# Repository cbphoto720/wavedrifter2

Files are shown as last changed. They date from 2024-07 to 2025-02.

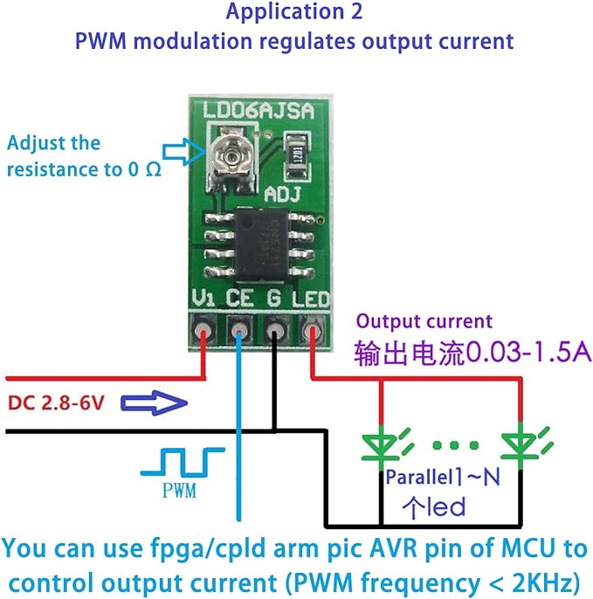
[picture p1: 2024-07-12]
Electronics/LED_driver.jpg

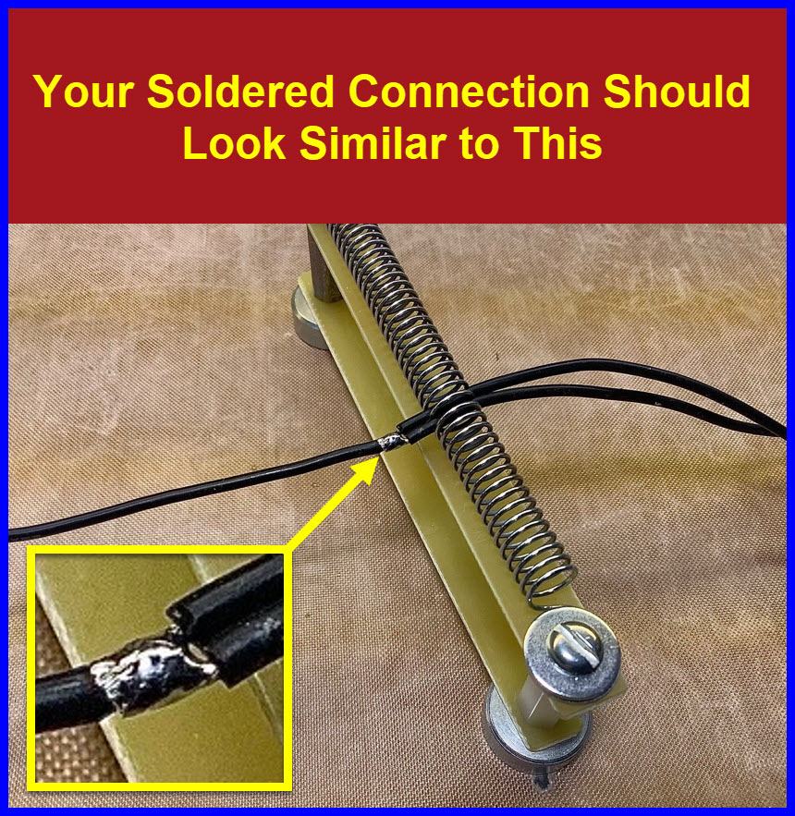
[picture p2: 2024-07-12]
Electronics/D.jpg

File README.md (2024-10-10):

# WIP
- [ ] LoRA underwater trails!! See [links on this page](https://www.thethingsnetwork.org/forum/t/lora-under-water/41144/26?page=2)
- [x] solder recovery LED to test on breadboard
- [x] more clearance for coin cell bat on sparkfun M8P board
- [x] FIGURE OUT GPS/ICM CONNECTION ISSUES
- [ ] write a new file if GPS / IMU log get too big?
- [x] Test the drifter2 Voltage sketch to see if it correctly reads the input voltage
- [ ] check which the best clock speed for teensy to run
- [ ] work on GPS buffer and timing
- [ ] work on more commands to send (beep 1s, recovery mode, flash LED 50% 1s)

- [x] Come up with solution for QWIIC connector issues
	- plug it in harder :)
- [ ] Come up with timing scheme for not overlapping GPS, IMU, and SD writes.  RFM broadcast needs to be its own thing.
- [ ] fix buf[99] vs buf[100] error that causes extra spaces
- [ ] SD card writing scheme that SAVES ON POWER DOWN
- [ ] write RAWX data to SD card (whole thing??? can the M8P make some UBX files?)
	- [ ] [write data to SD card efficiently](http://elm-chan.org/docs/mmc/mmc_e.html) and [also this one](https://stackoverflow.com/questions/25837386/read-write-binary-data-on-sd-using-arduino)
- [ ] BE CAREFUL USING RECOVERY LED AS SIGNAL LED (could draw too much current if PWM doesn't work)
- [ ] voltage divider to measure battery life
	- modify power battery connection to have a splitter for resistors and for the power board
	- **Low Voltage -> activate recovery mode**
	- **Extreme Voltage - > Shut down rover** (may only be able to do sleep mode)
	- design a power delivery pcb that has voltage monitoring, Hal effect sensor ON/OFF, and RFM filtering built in!
- [ ] 3DP new internalmounts 5.2
- [x] Manufacture drifter2.1
- [ ] Base station code to run into mission planner
- view GPS updates
- [ ] post photos and write assembly guide

# Code
### Speed
**RFM**
- test if using strlen is faster than using sizeof buffer.  (better to send the null chars or to calculate message size before sending it)

# Tests
- [ ] buoyancy test of drifter2.0
- [ ] buoyancy test of drifter2.1
- [ ] GPS underwater test
- [ ] RFM underwater test
# Nice-to-haves
- [ ]  design power/signal delivery pcb as a hat for teensy to make connections easier
- [ ] design new GPS antenna mount
- [ ] stronger mounting of IMU
- [ ] recovery LED mounting position
- [ ] [IMU FIFO buffer information](https://web.archive.org/web/20240229060544/https://wolles-elektronikkiste.de/en/icm-20948-9-axis-sensor-part-ii)
____
- [x]  cut the red wire inside one of your microUSB cables.  Use jumpers and power supply to spin up the box
- RFM69 should be power by teensy onboard 3V supply (Likely cleaner than the FlipFlop board)
- [x]  Internal mounts is just slightly too tall.  take off 0.5 or 1mm and include a cutout for the Teensy 4.0 backing SMD electronics.
- [ ] add mounts for Status LED, Recovery LED, Buzzer
- [ ] [RAWX message structure](https://docs.ros.org/en/noetic/api/ublox_msgs/html/msg/RxmRAWX.html)
- [x] u-center M8P config
	Only output NEMA strings and RAWX data
	[10Hz U-blox binary GPS data in 66 lines of code (arduino)](https://www.youtube.com/watch?v=TwhCX0c8Xe0&t=0s)
	save configuration so that it can be uploaded to each board.  (have arduino read a ublox startup file???  That would be the cleanest way to ensure the boards are config ready)
	then work on arduino parsing of the hex binary
- [ ] Interrupt based programming routine so that you know when the buffer is being used!  (dont want to have another message write over the buffer before you read it!)
	have a routine handle the interupt code before returning to what you are doing.
	- look up simple arduino examples of interupts
- [ ] [RFM69HCW datasheet](https://cdn.sparkfun.com/datasheets/Wireless/General/RFM69HCW-V1.1.pdf) Page 48 describes DIO mapping in order to select what type of interrupt you would like to know about the buffer.  This is useful for Interrupt routines to handle saving the data

- [ ] Write code to test RFM 
- [ ] test broadcast with different drifter SG & range
- [ ] Another test of speed by broadcasting IMU data live
- [x] Do not work on HousingMounts until you finalize what electronics you need.  (3d printed inside)
	top of battery can sit 16mm from the top of 2-140_UP internalring.
	O-ring crossed & stretched 10mm from top of arduino board
- [ ] Code that detects a large upsurge in waves (perhaps a good time to broadcast/look for GPS on the crest of a wave???)

- [x] UPDATE FALK
	- Housing final size
		- USE [F9P board](https://gnss.store/zed-f9p-gnss-modules/145-195-elt0128.html#/61-gnss_module-l1_l2_zed_f9p) to achieve a 2mm increase in size (smaller battery size too)
	- internal board mount
	- Transceivers are communicating
		- what if the board would receive GPS, Broadcast that is got a hit, then trigger a camera to take a picture as fast as possible since GPS aquisition
	*Questions
	- ask for 3dp company name
	- show code running

###### Housing
- [ ] PCBway 3d print: Somos Ledo resin + UTR-8100 (Translucent) (See if the spray varnish option changes the O-ring dimensions!)
- [x] Finish GPS mount with space for reed switch + LED + RFM board
- [x] place to mount flip flop board
- [x] place to mount buzzer somewhere
- [x] place to mount battery O ring hooks on M8P board
- [x] FLIP SCREWS they wont fit unless the nut is face up

- [x] build in tolerance for inner mating halves
- [x] build in tolerance for o-ring groove (for using a HSS lathe tool to make face grooves)??? **Decide if you are going to use the lathe**

- [x] how to connect lipos (and how to charge)
- [x] find a reed switch/ HAL sensor

- [x] mount board internals

###### Electronics
- [x] solder RFM69HCW boards to propotying pins
- [x] test transceiver boards (follow [this guide](https://learn.sparkfun.com/tutorials/rfm69hcw-hookup-guide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))
- [x] Work on HAL sensor board
- [x] Power solution for M8P + transmitting mssg (current draw getting close to 250 mA)
	- [x] power M8P through USB connector if needed (tap directly into battery through hall effect sensor switch board)
##### FIXME

# Ideas
**Transciever ideas**
- void setup:
	broadcast Drifter#, Voltage, IMUfilename, GPSfilename
- Recovery mode
	activate internal buzzer
	increase RFM broadcast Hz
	activate LED
- Wave-detect transmission
	look at IMU data to detect a wave, use wave as an opportunity to transmit/look for GPS from a taller height off the water
# Componets
- VHB tape: 0.4" x 0.025" (10.16 x 0.635 mm)
## GPS
**glonass**
- 1598-1604 MHz
- GPS 1575 MHz L1

[SMA to U.FL connector](https://www.coaxrf.com/shop/4uflcables/smaconnector/gold-plated-sma-male-plug-to-ipx-u-fl-male-plug-center-rf-adapter-connector/) $5.49

[GNSS OEM F9P board ](https://gnss.store/zed-f9p-gnss-modules/145-195-elt0128.html#/61-gnss_module-l1_l2_zed_f9p)
**L1/L2 Antennas**
- [AHP2258.07.0060A](https://www.taoglas.com/product/active-gnss-l1-l2-band-antenna/) TAOGLAS (slightly too big with PCB) (70x70mm ground plane)
- [ 2JM3201C2F ](https://www.2j-antennas.com/antennas/single-internal-antennas/2jm3201c2f-high-precision-gnss-gps-beidou-galileo-glonass-sbas-rtk-l1-l2-active-stacked-patch-internal-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) 2J Antennas GREAT SIZE (slightly worse but tested W/O groundplane!)
- [ANT1825JB01BGNL2A](https://www.digikey.com/en/products/detail/pulse-electronics/ANT1825JB01BGNL2A/15290928) not a lot of datasheet (TOO BIG MOQ)
- [HP2258.A](https://www.digikey.com/en/products/detail/taoglas-limited/HP2258-A/21777748) Taoglas PASSIVE L1/L2
- [APRG2512F01](https://www.digikey.com/en/products/detail/abracon-llc/APRG2512F01-0100S/15912595) Good datasheet
### Transmitter
- [sparkfun dev board](https://www.sparkfun.com/products/15005)
###### Alternative hardware
- [Ublox NEO-M8P-0](https://www.digikey.com/en/products/detail/u-blox/NEO-M8P-0/6150644)
	- Smaller footprint than ZED-F9P
	- Low power (~35mA [ICC Acquisition. Average current from startup until the first fix])
	- 3V

- [mini usb dev board](https://gnss.store/neo-m8p-gnss-modules/90-elt0078.html)

### Antenna
- [TAOGLAS AGGP.25f](https://www.digikey.com/en/products/detail/taoglas-limited/AGGP-25F-07-0060A/3083243) dual 1.575/1.602GHZ PATCH with U.FL connector.  High beam width for more tilt tolerance

###### RF tranceiver
- [sparkfun transciever](https://www.sparkfun.com/products/13909) 915 or 434MHz comms (500m range in open air)  can remotely activate drifters, receive position, or use an [activate an LED](https://www.mouser.com/ProductDetail/Cree-LED/XPEWHT-L1-0000-00D01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)  (time lapse of wave)
###### Combo antenna GSM / GPS
- internal circumference 188mm
- 1.2 to 1.6 GHz

- [Smallest combo ant](https://www.digikey.com/en/products/detail/te-connectivity-linx/ANT-LPC-FPC-100/10663172) 64mm long
- [ Molex](https://www.digikey.com/en/products/detail/molex/2133530100/11673870) flexible 119mm with 2 U.FL
- [Ceramic patch style](https://www.l-com.com/embedded-active-gps-gsm-3g-antenna-3dBi-5dBic-ufl-hg821-03pu-gps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) 42mm square ground plane
-[ TAOGLAS flex ant](https://www.digikey.com/en/products/detail/taoglas-limited/FXUB70-A-07-C-001/4965533) 150mm long
- [BIG external TAOGLAS](https://www.mouser.com/ProductDetail/Taoglas/MA104.C.AB.015?qs=Ajmft%252BTTukF16yQE2i0Gfw%3D%3D)
###### Alternative hardware
- [page 24](https://content.u-blox.com/sites/default/files/NEO-M8P_HardwareIntegrationManual_UBX-15028081.pdf) of ublox handbook reccomends GPS antenna
	- https://www.tallysman.com/product/tw3400-single-band-gnss-antenna/
	- https://www.digikey.com/en/products/detail/taoglas-limited/GP-1575-25-4-A-02/2332642 (i found this patch antenna through a 1.575GHz digikey filter)
	- https://www.digikey.com/en/products/detail/taoglas-limited/A-40-A-301111/4503583

**Patch antennas**
- [Taoglas](https://www.digikey.com/en/products/detail/taoglas-limited/AP-25F-07-0078A/2754153) 3" U.FL cable (SAW, LNA, LNA) (medium size)
- [Taoglas AP.10F.07.0039B](https://www.digikey.com/en/products/detail/taoglas-limited/AP-10F-07-0039B/3083256) 1" U.FL cable (SAW, LNA, LNA) (smallest package)
- [Taoglas AGGP.25F.07.0060A](https://www.digikey.com/en/products/detail/taoglas-limited/AGGP-25F-07-0060A/3083243) (13 grams, first one I ordered)
- [ a med sized offering AP.12F.07.0045A](https://www.digikey.com/en/products/detail/taoglas-limited/AP-12F-07-0045A/3877418) (wonky radiation pattern)

### Reed switch
- look for latching magnetic reed switch

- [potential option](https://www.mouser.com/ProductDetail/MEDER-electronic-Standex/KSK-1E66-1-BV14501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) (expensive $10)
- [potential ](https://www.digikey.com/en/products/detail/tdk-micronas-gmbh/HAL1502%2520UA/18151531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)(HAL effect switch) HAL 1502
	- use with a relay ([maybe this relay](https://www.digikey.com/en/products/detail/cui-devices/SR5-5V-200-1C/16602072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))
	- google "1a relay through hole 5v"
	- [low profile relay option?](https://www.digikey.com/en/products/detail/panasonic-electric-works/TQ2-L-3V/304092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)
	- [another option](https://www.digikey.com/en/products/detail/omron-electronics-inc-emc-div/G5V-1-T90%2520DC24/6650357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)
	- [low power consumption option?](https://www.digikey.com/en/products/detail/cui-devices/SR5-3V-200-1C/16602081)
	- [Flip Flop switch instructions for MCU sleep](https://www.hackster.io/usini/easy-way-to-put-your-board-to-sleep-5184a2)
	- 
- [Sparkfun latching HAL sensor](https://www.sparkfun.com/products/9312)
- [Sparkfun Reed switch non-latching](https://www.sparkfun.com/products/8642)
- [latching reed switch](https://www.layouts4u.net/electrical-items/switches/latching-reed-switch#:~:text=is%20in%20stock%3F-,Latching%20Reed%20Switch,again%20to%20switch%20it%20off.) with magnet on the outside?

## Batteries
- 3.4 V cutoff voltage

**Old bat**
- [250mah lipo](https://www.amazon.com/EEMB-Battery-Rechargeable-Lithium-Connector/dp/B08FD3V6TF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)

**New Bats**
- [820mah](https://www.amazon.com/EEMB-653042-Rechargeable-Connector-Certified/dp/B082152887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) 44x30.5x6.8mm
- [2000mah](https://www.amazon.com/EEMB-2000mAh-Battery-Rechargeable-Connector/dp/B08214DJLJ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) 56x34.5x10.6mm
- [1100mah](https://www.amazon.com/EEMB-1100mAh-Battery-Rechargeable-Connector/dp/B08FD39Y5R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) 51x34.5x6mm
- [tiny 500mah can fit up to 3](https://www.digikey.com/en/products/detail/tinycircuits/ASR00035/9808767)
- [Tiny 290mah (a little smaller than the 500)](https://www.digikey.com/en/products/detail/tinycircuits/ASR00007/7404517)
- alternative 500mAH supplier [bulk pricing](https://tinycircuits.com/products/lithium-ion-polymer-battery-3-7v-500mah)

[Website for all shapes of battery](https://www.lipolbattery.com/lithium%20polymer%20battery.html): LP883648 is 1600mAH and 48mm longest dimension

## Housing
- [BAL TEC](https://www.precisionballs.com/pictgal.php#hollowsteel) Potential manufacturing source?  Makes all kinds of spheres'
- google search terms "cnc machine sphere hollow"
- [MACRO RING cam filter](https://www.amazon.com/dp/B08XMLK592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) Closure plate for interface?
## CLOSURE SYSTEM

Inspiration:

- https://www.indiamart.com/proddetail/stainless-steel-pipe-clamp-16592394673.html
- https://www.mscdirect.com/product/details/04700365
- THIS IS THE BEST ONE https://www.aliexpress.us/item/2255800979747014.html?gatewayAdapt=glo2usa4itemAdapt
- https://www.grainger.com/product/5DFH4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
- https://www.amazon.com/Stainless-Strengthens-Circular-Fasteners-Clamps/dp/B0B35VBNF4
- binder clip?
- [Hose clamp style with cross dowel nuts](https://www.amazon.com/Stainless-Strengthens-Circular-Fasteners-Clamps/dp/B0B35VBNF4?th=1)
- [Stainless cross dowel nuts](https://www.aliexpress.us/item/3256804059479775.html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)
- WALMART [pipe clamp](https://www.walmart.com/ip/Adjustable-pipe-clamp-hose-clamp-quick-release-round-duct-clamp-quick-pipe-clamp-barrel-clamp-ring-SS-galvanized-80-400mm-dia/1670025789)

**3d Printed inspiration**
- [Aquarium clamp](https://www.reef2reef.com/threads/uv-pipe-clamps.633090/)
- [gopro pipe clamp](https://www.instructables.com/GoPro-Hinged-Pipe-Clamp/)
- [SLS print service](https://www.artisanmodelmakers.co.uk/blog/portfolio-items/3d-printed-automotive-parts/)

## O-RINGS
Housing2_rev2 uses a 2-224 o-ring

- -036 rings are too small diameter (similar to what Falk used)
- 2-142 ID close to 60mm  https://www.mcmaster.com/9452K148/
- should increase o ring size for better sealing
- these 60mm metric rings are a better because they are 50A shore hardness https://www.mcmaster.com/2418T185/

**50a Durometer**
- Grainger [2-146 50A o ring](https://www.grainger.com/product/O-Ring-146-712U13)
- Mcmaster [2-231](https://www.mcmaster.com/2418T186/) or [2-230](https://www.mcmaster.com/2418T185/)
  Mcmaster [2-146](https://www.mcmaster.com/2418T161/) Don't go this small unless you really need to

## LED
- [1.5 W COB LED](https://www.digikey.com/en/products/detail/creeled,-inc./JK3030AWT-P-H50EA0000-N0000001/9974567?utm_adgroup=&utm_source=google&utm_medium=cpc&utm_campaign=Pmax_Shopping_Boston%20Metro%20Category%20Awareness&utm_term=&utm_content=&utm_id=go_cmp-20837509568_adg-_ad-__dev-c_ext-_prd-9974567_sig-Cj0KCQjw0_WyBhDMARIsAL1Vz8t7g8jTEnTvU7pAn2EhZ3dJouXCVCa7Tl-RsGRhepSoWFnkOTOHie8aAs1fEALw_wcB&gad_source=1&gclid=Cj0KCQjw0_WyBhDMARIsAL1Vz8t7g8jTEnTvU7pAn2EhZ3dJouXCVCa7Tl-RsGRhepSoWFnkOTOHie8aAs1fEALw_wcB) run with arduino +extra flip flop board.
- [0.5W LED amazon](https://www.amazon.com/dp/B01CUGACEA/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)

# Programming

### 20240424 Talking with Brian
- 915 mHz band is usually multiplexed frequency hopping.  You don't see all that behind the scenes stuff.
- 2 ways to do it
1. Have the master emit a call that asks a drifter for a transciever update.  (advantage that the timing always works out) (disadvantage: teensy has to be collecting data and listening for master at same time)
2. Have the Teensy collect and collect data and then brief pause to cast out their mssg when it is their time slot.  You have to sync with GPS time.  (maybe even having the base broadcast the most recent GPS time could be an advantage)
### RFM69HCW
[Hookup guide](https://learn.sparkfun.com/tutorials/rfm69hcw-hookup-guide/hardware-overview)
- [Tips for teensy guide](https://forum.pjrc.com/index.php?threads/rfm69w-rfm69hw-transceiver-t3.24576/page-3#post-47264)

[RFM69 Git Library LowPowerLab](https://github.com/LowPowerLab/RFM69)

TRANSMIT MESSAGE:

| D# (Drifter #) | STATUS ('STR' Startup, 'LOG' (recording data), 'REC' (recovery), 'OFF' (shutdown)) | LAT | LON | age (GPS data) | Bat voltage |
| --- | --- | --- | --- | --- | --- |
**ATC - Auto Transmission Control**
- set RSSI floor to at least -60dBm, may want to disable to not try to broadcast too quietly
- [Regulater PSU tutorial sparkfun](https://www.sparkfun.com/tutorials/103)
- 
**CSMA**
- transceiver LISTENS before it tries to TALK.  If 2 radios are actively listening to each other, another raido can mess things up by trying to talk over

**Sparkfun m8p**
- Must ALWAYS be trying to aquire a satellite.

# Solidworks

### Housing2_Boss
- internal sphere radius will need clearance for mating feature

**Mechanical:**

- Talk to Kent about Grinding our own HSS groove tool
- Hemisphere half #2 could have an internal lip to improve mating strength
- 50A durometer O-ring and 1/8" cross section would give us the best change with our space.  Could drop to a 3/32 o-ring if space is required.  (Drifter #1 was 70A durometer, 1/16 ring with an improper groove design) 
- 1mm clearance on o-ring groove (need to make battery decision to reduce O-ring size

# References
- **[minimal-arduino-mavlink-example](https://github.com/patrickelectric/minimal-arduino-mavlink-example)** Code to connect teensy to MissionPlanner

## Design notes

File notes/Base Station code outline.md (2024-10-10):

## Init
- [x]  track num of drifters
- [x]  buffer that tracks the last comm record for each drifter.
## Startup
- [x] connect to mission planner
- [ ] start RFM
- [ ] Broadcast Base UTC time (rfm 255 broadcast to all)

## Loop
- [x] heartbeat
- [x] report drifter health & location
- [ ] send drifter commands (recovery, shutdown, etc.)
- [ ] track last time drifter reached comms

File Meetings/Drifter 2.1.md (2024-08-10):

## Updates
- Drifter 2.1 is operational.
	- Everything is barebones.  Drifter is collecting IMU, RAW GPS, and NMEA GGA data and can broadcast any info we need back to base station.
- 
- Working on MAVLink code to polt data in MissionPlanner
- Working on Bat voltage sensor

## WIP
- Base station in MissionPlanner app
## Questions
- is there any budget left to spend?
	- [ ] new HAL effect sensors (non-latching) (or just design better clearance for the reed switches)
	- [ ] more mini GPS antenna
	- [ ] Passive components (capacitors, Power delivery PCB board? {rout power, caps for RFM, HAL effect sensor SMD})
- Any experience with Sparkfun QWIIC cables?  I am leaning toward soldering everything Point-to-point
-

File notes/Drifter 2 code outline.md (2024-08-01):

### SPI
- microsd
- Transceiver
### I2C
- imu
- GPS
##### Key
//WIP - Things to fix!
//FLAG - Important note
//DEBUG - useful for problem solving
//BLINK - good spots to communicate to user what is happening
//OFF - places where the program should shut down (may be able to reset with Flip-Flop board)
//ERROR - places where an error should be thrown

# WIP
- [x] use struct NMEA_GNGGA to parse data ([follow this tutorial](https://www.youtube.com/watch?v=ylxwOg2pXrc&t=0s)) and then broadcast valid fix lat/lon to base
- [ ] find a way to interally store RAWX in M8P LOG file before writing to SD card
	- [ ] exactly what data needs to be written to the card.  Is it the full RAWX binary every time or can we slim it down?
- [ ] broadcast from 915 mHz
	- why can it read transmissions but not ACK or Broadcast on its own?
- [ ]  Log data to microsd
	- [ ] IMU data format
	- [ ] GPS NMEA strings
- [ ] voltage divider to activate Recovery mode
- [ ] receive messages from BASE to activate other sampling modes

**SD_ReadWrite_example3**
- Working prototype of reading/writing data
- Definite connection issue on the breadboard creating weird null characters, even in the SD card FILENAME (a const char).  I am hoping these missing characters are just a connection problem on the breadboard.
**Drifter2.ino**
- determine when to blink LED and what color for indication (look for //BLINKS in code)
- [x] Write code to create the filename for each drifter (here is a good forum post that has a [file naming sprinrf](https://forum.arduino.cc/t/create-variable-text-file-name-to-be-saved-on-sd-card/1158544/3))
- [ ] change gatherIMUdata (160) to ONLY collect data
	- write function to print IMU data once stored in a buffer of sufficient size

**NEO M8P TX-ready indication**
- super useful for interrupt based programming! [Ublox M8P RecieverDescrProtocol](https://content.u-blox.com/sites/default/files/products/documents/u-blox8-M8_ReceiverDescrProtSpec_UBX-13003221.pdf)
	UBX - CFG - PRT (configure PIO port to Tx ready with kb threshold set)
	UBX - MON - HW (monitor Hardware to see PIO assignments)

___
# Functions
- Parse GNGGA -> see readme in drifter2

# VOID SETUP
**microSD card**
- [x] begin serial
- [x] checkIMU
- [x] init SD card /currently ugly
- [x] calibrateIMU
- [x] initialize files
- [x] make filename "drifterXX_log000X.txt"
- [x] choose max file size (Battery life should automatically limit these files to an acceptable amount)
- [x] init GPS
- [x] initialize GPS settings (set up from default (NMEA messages, RAWX, TX-ready interrupt, Nav Freq 4Hz, Full power mode)
	https://www.youtube.com/watch?v=TwhCX0c8Xe0&t=1025s
	https://www.youtube.com/watch?v=ylxwOg2pXrc&t=20s
	https://www.youtube.com/watch?v=n8PUyOtiGKo
	one of these videos shows how to send UBX messages over I2C or at least something similar.
	- [ ] Log UBX-RAWX data ([data structure](https://content.u-blox.com/sites/default/files/documents/u-blox-F9-HPG-1.32_InterfaceDescription_UBX-22008968.pdf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) page 189 in the zed F9 manual)
- [ ] check the 915 mHz
- [ ] check comms with base station
- [ ] buzz to indicate data logging
- [ ] send mssg to base station when logging

# VOID LOOP
- [check voltage every](https://www.youtube.com/watch?v=gw72g4WBz-U) so often, activate a deep sleep state and the buzzer at some critical voltage level
- [ ] use microNMEA to read lat/long/time from drifter and send comm mssgs back on the RFM69
- [ ] attach interrupt for GPS to say it has new data
	Interrupt could simply set a flag to process the GPS data in the main loop
- [ ] attach interrupt for RFM when receiving data from BASE
- [ ] periodically (40ms) log IMU data
- [ ] periodically send 915 mHz mssg

___
# Base station code outline
- [ ] include all libraries

**Initialize**
- [ ] Drifter ID=0
- [ ] broadcast power

###### Specialize commands
- [ ] Calibrate IMU while in housing
- [ ] Activate sleep state (Disable GPS (may not be able to do that because GPS=UTC time clock, how will it know when to send messages?  Maybe it just won't be talking.  See how much the RFM69 draws when it is just listening for signals))
- [ ] Request data download

# Base station GUI
- [ ] KML position map of all drifters
- [ ] Drifter status list
	- [ ] battery %
	- [ ] Time since last communication
	- [ ] Time since last GPS fix
	- [ ] Time spent powered on
- [ ] send commands
	- [ ] [[#Specialize commands]]

- [ ] read serial interface mssgs from base
# Questions
- What information is required for RAW GNSS messages in order to do PPK?

# Datalog
```
\\\\\\\\\\\\\\\\\\\\ NEW START \\\\\\\\\\\\\\\\\\\\ 
\\Drifter_Number(DRIFTERNUM)_(FILENUM).txt
\\Bat Volt: (VOLTAGE) V, 
\\IMU_update: (IMUupdate) ms, GPS_update: (GPSupdate) ms, Transciever_update: (TRANSupdate) ms
\\ Accel_range: (ACCELrange)G, Gyro_range: (GYROrange) dps
\\ IMUtime, Ax, Ay, Az, Gx, Gy, Gz, Mx, My, Mz, P, T
\\ NEMA MSSG: $GPGGA,UTCtime,Latitude,N,Longitude,W,GPS_Quality,#SVs,HDOP,MSL_height,M(meters),Geoid-seperation,M(meters),Age_of_differentialGPS,Ref-StationID,*Checksum
// RAWX MSSG:
$RAWX GNSS_ID,SV_ID:,Psuedorange(meters),CarrierPhase(cycles)

```

# Examples
**SparkFun_u-blox_GNSS_Arduino_Library\examples\ZED-F9P\Example23_getRXMRAWX**
- get RAWX GPS messages Psuedorange and Carrier Phase info
GNSS ID: 0     SV ID: XX     PR: XXXXXXXX.XXX m     CP: XXXXXXXXX.XXX cycles

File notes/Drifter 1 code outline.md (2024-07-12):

***
- it seems GPS is ONLY used for time
- GPS read can easily cause a hang by waiting for lasteNEMAread command

***
- [ ] include all libraries

#### Initialize
- [ ] debug mode (serial output, etc)
- [ ] time=0
- [ ] Drifter ID = XX
- init pins
	- [ ] LED
	- [ ] MicroSD CS
	- [ ] GPS CS
	- [ ] IMU pins

- [ ] IMU interval
- [ ] GPS interval
- [ ] MicroSD interval
- [ ] Broadcast interval

**IMU calibration**
- magnetic, accel, gyro
- set accel ranges
- set gyro range

#### Functions
- calibrate IMU (manually sets the offsets from a static test)
	- was this only performed for 1 board than applied to every IMU??
	- accel range was set to 16G
- gatherIMUdata: read IMU sensor and .print 
	- file is only closed (file.flush) every 200 writes (40ms * 200 = 8s)
	- this is only assuming that the void loop doesn't experience any delays, it could be even longer
- checkSD: Check SD card is active
- createheader: Create file header for readability
- spacer: formats the correct number of " " characters based in number size
	- couldn't the file be seperated by character delimiters like tabs instead?

#### Void Setup
- run all setups and calibrations
- Turn LED on at the end of setup
	- if LED is off, Setup had failed

#### Void Loop
- very start of loop first thing
- currentTime= millis()
	- Wouldn't this just overwrite any GPS time
	- (yes it does, but the later code writes down the GPS corrected time if it is different than the lastGPStime).  Which means if more time has passed than the given GPS_UPDATE, the GPS function is ran: microcontroller time is printed and then the last NEMA message is printed as comparison.  LastGPStime is then updated to the current MICROCONTROLLER time.
	- It seems like the GPS time is not at ALL interacting with the internal clock and is only providing reference to UTC for post processing.

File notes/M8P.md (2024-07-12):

- Update firmware.  FIS = flash.xml in u-center program folder
- Use reciever configuration to send RAWX and NEMA mssgs

[GNRMC mssgs](https://openrtk.readthedocs.io/en/latest/communication_port/nmea.html) could be useful because they have a A=effective positioning flag that indicates GPS positioning is vaild.

### Config Binary Messages
```
// Configure I2C UBX+NMEA and enable Tx_ready on EXTINT with 43 byte threshold and then SAVE CFG
{0xB5, 0x62, 0x06, 0x00, 0x14, 0x00, 0x00, 0x00, 0xB5, 0x15, 0x84, 0x00, 0x00, 0x00, 0x00, 0x00, 0x00, 0x00, 0x03, 0x00, 0x03, 0x00, 0x00, 0x00, 0x00, 0x00, 0x6E, 0xD1, 0xB5, 0x62, 0x06, 0x09, 0x0D, 0x00, 0x00, 0x00, 0x00, 0x00, 0xFF, 0xFF, 0x00, 0x00, 0x00, 0x00, 0x00, 0x00, 0x03, 0x1D, 0xAB};
```

```
// Configure I2C UBX+NMEA and enable Tx_ready on EXTINT with 8 byte threshold on a FALLING trigger
{0xB5, 0x62, 0x06, 0x00, 0x14, 0x00, 0x00, 0x00, 0xB7, 0x00, 0x84, 0x00, 0x00, 0x00, 0x00, 0x00, 0x00, 0x00, 0x03, 0x00, 0x03, 0x00, 0x00, 0x00, 0x00, 0x00, 0x5B, 0x90}
```

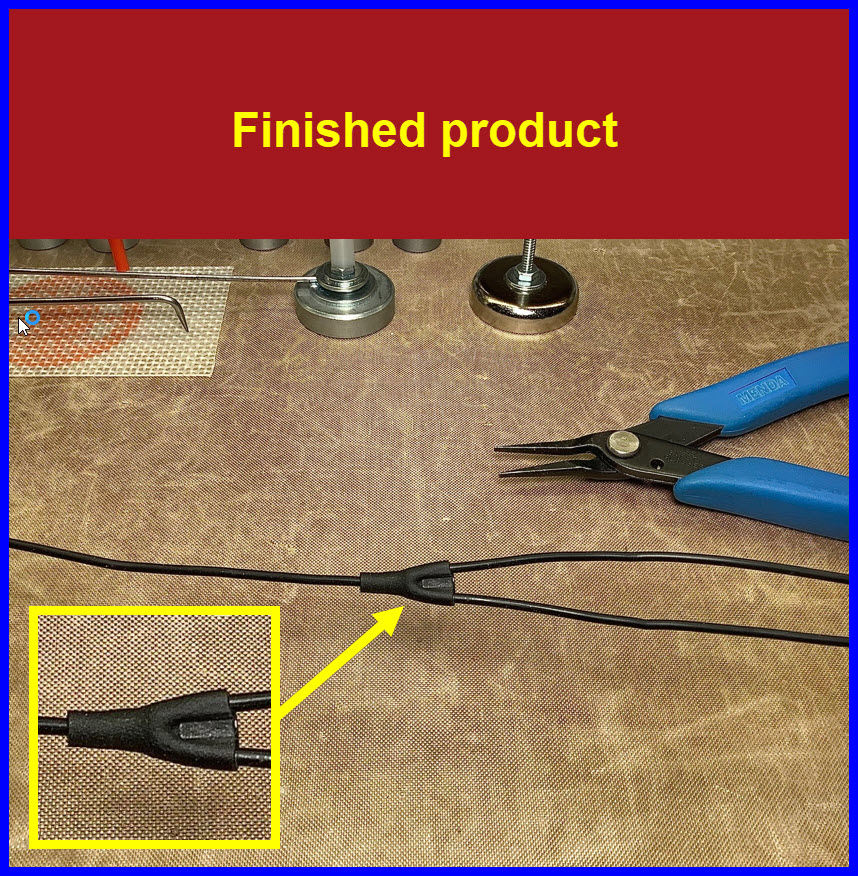
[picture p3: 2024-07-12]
Electronics/F.jpg

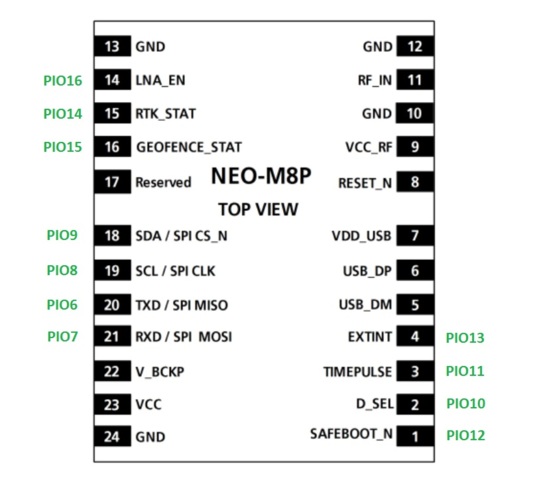
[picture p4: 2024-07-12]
Electronics/M8P/M8P_PIOvsPIN.jpg

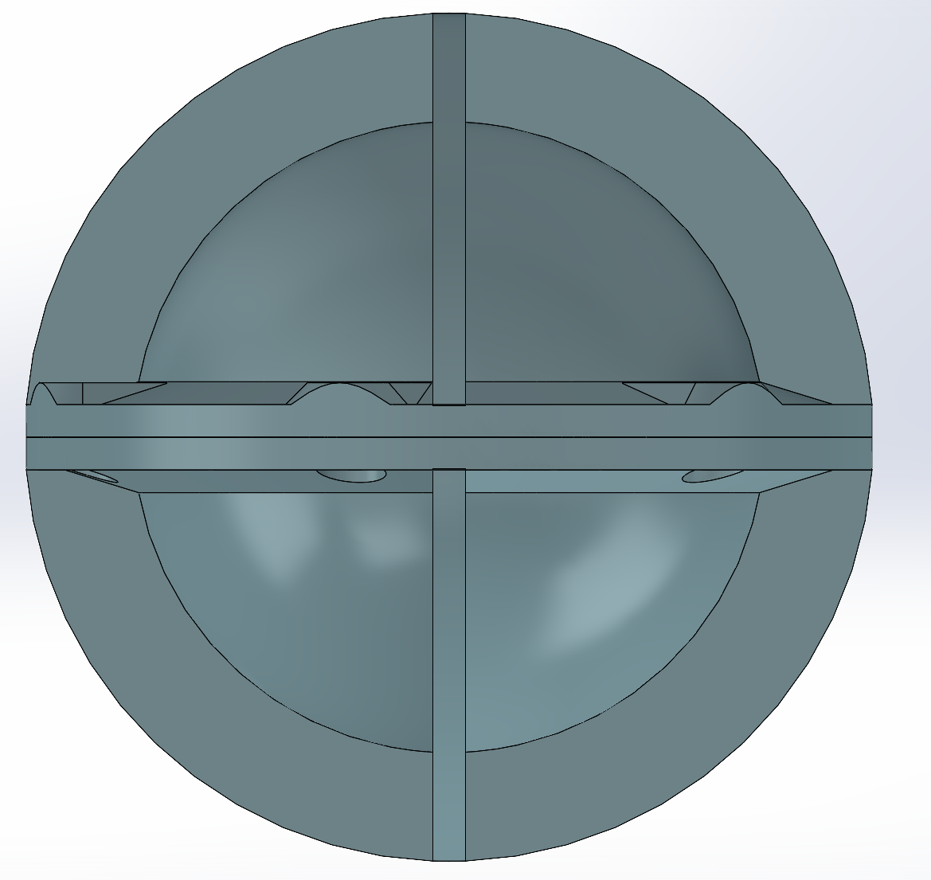
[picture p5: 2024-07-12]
Renders/Screenshots/20240411_Drifter2_HousingFinal.png

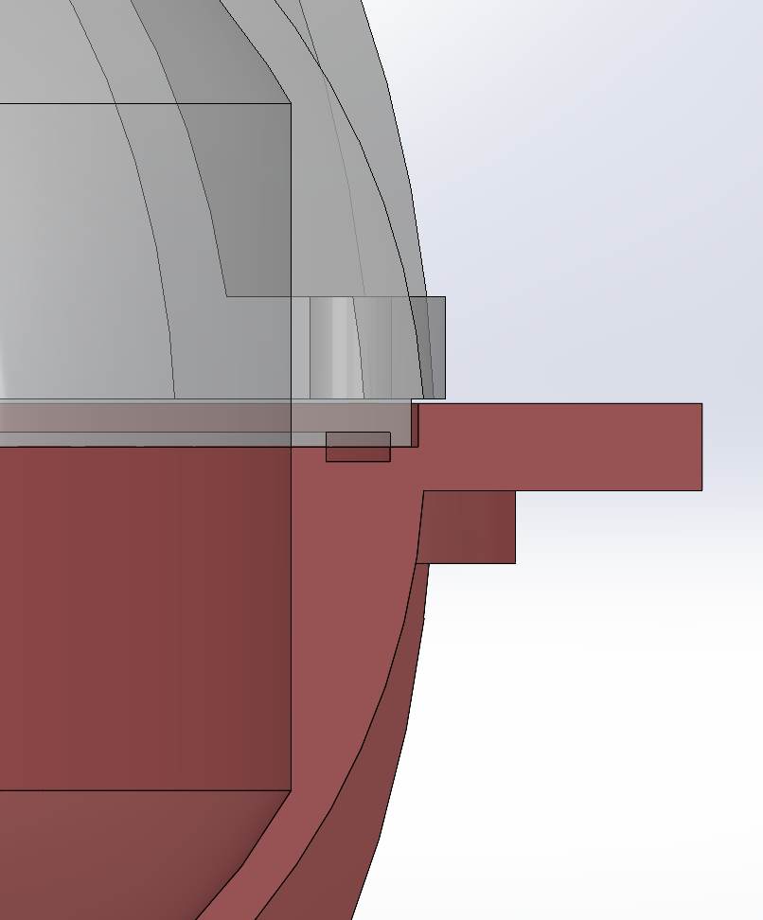
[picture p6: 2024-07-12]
Renders/Drifter1_o-ring_cutaway.png

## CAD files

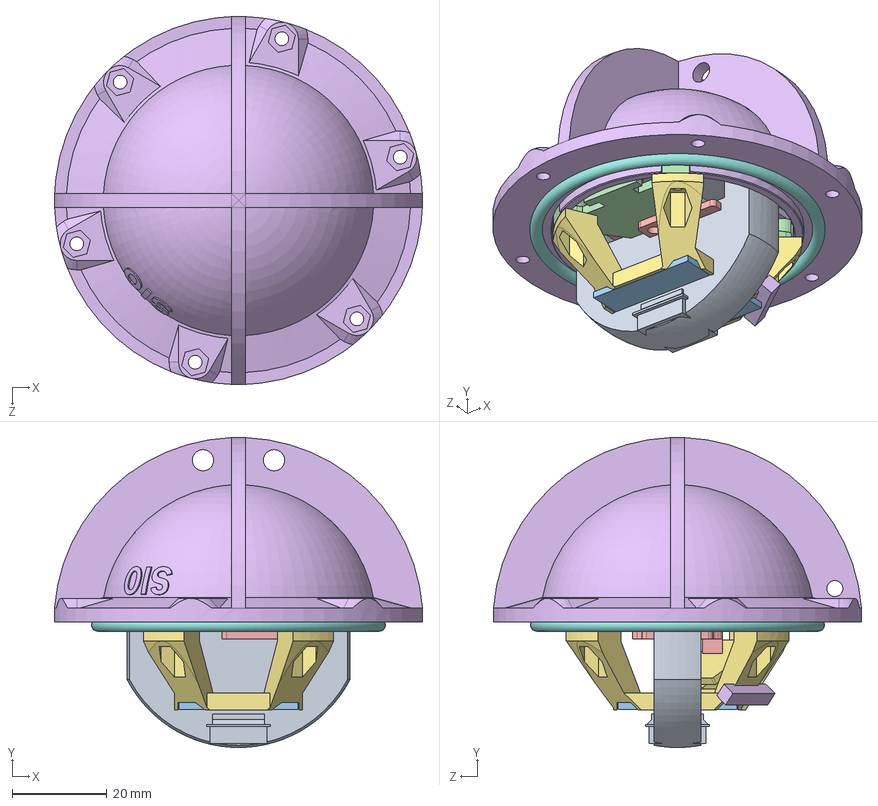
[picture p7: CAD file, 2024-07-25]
Drifter2_Assem1_LOWCG.SLDASM
77.7 x 65.5 x 77.7 mm
Sparkfun_NEO-M8P
Teensy_4-0
Battery_AllSizes_configurations
internalmounts
Pimoroni_ICM20948
housing2_rev2
Sparkfun_RFM69HCW_transceiver
2418T159_Oil-Resistant Soft Buna-N O-Rings
92290A060_Super-Corrosion-Resistant 316 Stainless Steel Socket Head Screw
94205A101_316 Stainless Steel Nylon-Insert Locknut
Internalmount5_housingmount
FlipFlopBoard
reedSwitch
InternalMounts5_GPS_Cradle
microSDreader
TAOGLAS_AP12F070045A
1W-LED_280mA_Xiaoyztan
internalmounts5_GPS_minicradle

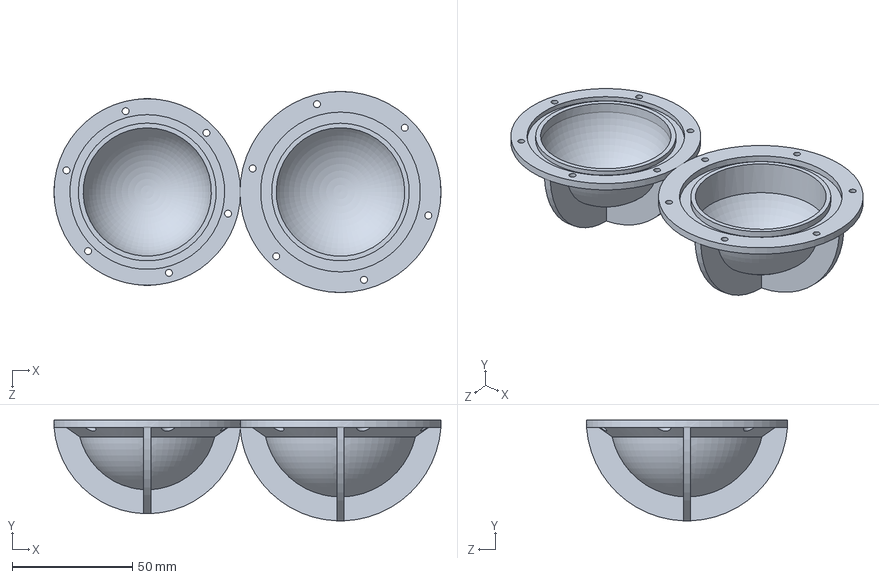
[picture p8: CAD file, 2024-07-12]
Housing_Rev2_comparison.SLDASM
161.2 x 42.0 x 83.7 mm
housing2_rev2 x 2

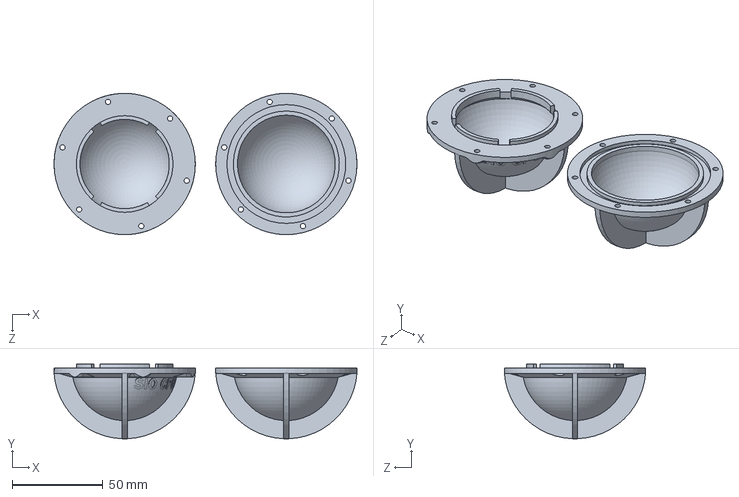
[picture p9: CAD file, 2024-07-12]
Housing_comparison_Prototype.SLDASM
166.6 x 41.0 x 77.7 mm
housing2_rev2 x 2

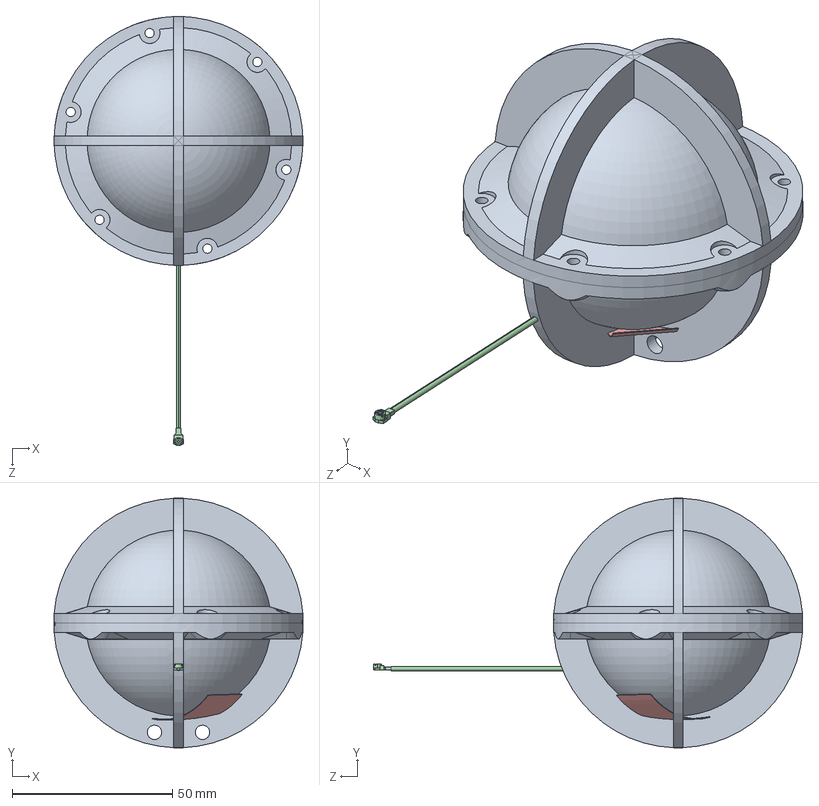
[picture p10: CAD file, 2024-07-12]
Drifter2_Assem_F9P.SLDASM
77.7 x 77.9 x 134.0 mm
Teensy_3-2
Battery_AllSizes_configurations
internalmounts
Pimoroni_ICM20948
housing2_rev2 x 2
Sparkfun_RFM69HCW_transceiver
GNSSOEM_ZEDF9P_ELT0128
2jm3201c2f.step

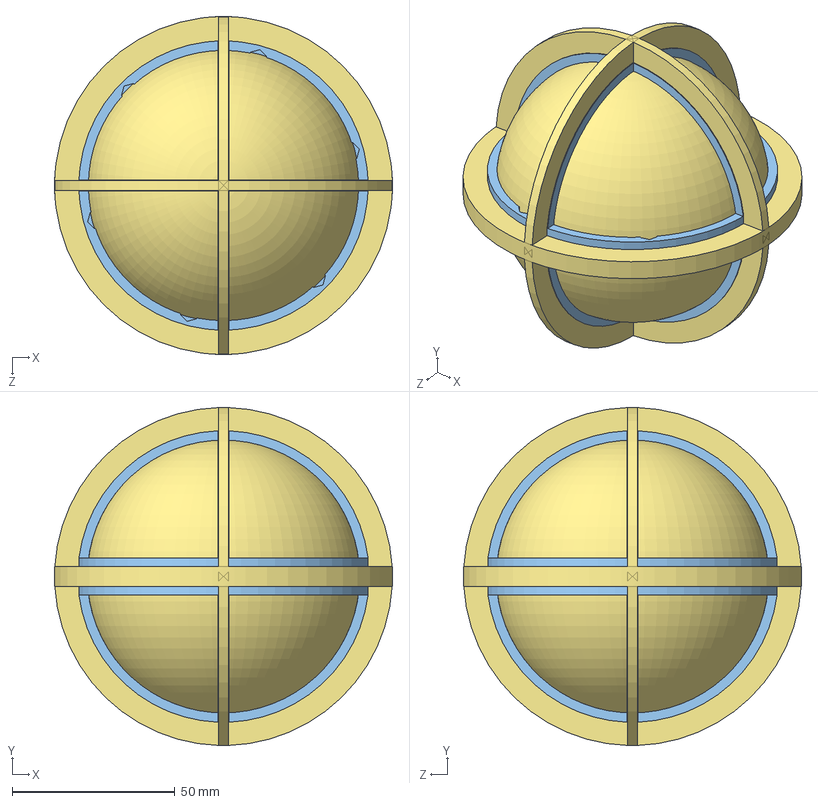
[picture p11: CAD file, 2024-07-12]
Drifter2_Assem_GSM.SLDASM
104.0 x 104.0 x 104.0 mm
Sparkfun_NEO-M8P
Teensy_3-2
EXVIST_4GLTEGSM_EC25-AFX
Battery_AllSizes_configurations x 3
MA104.C.AB.015
BALL

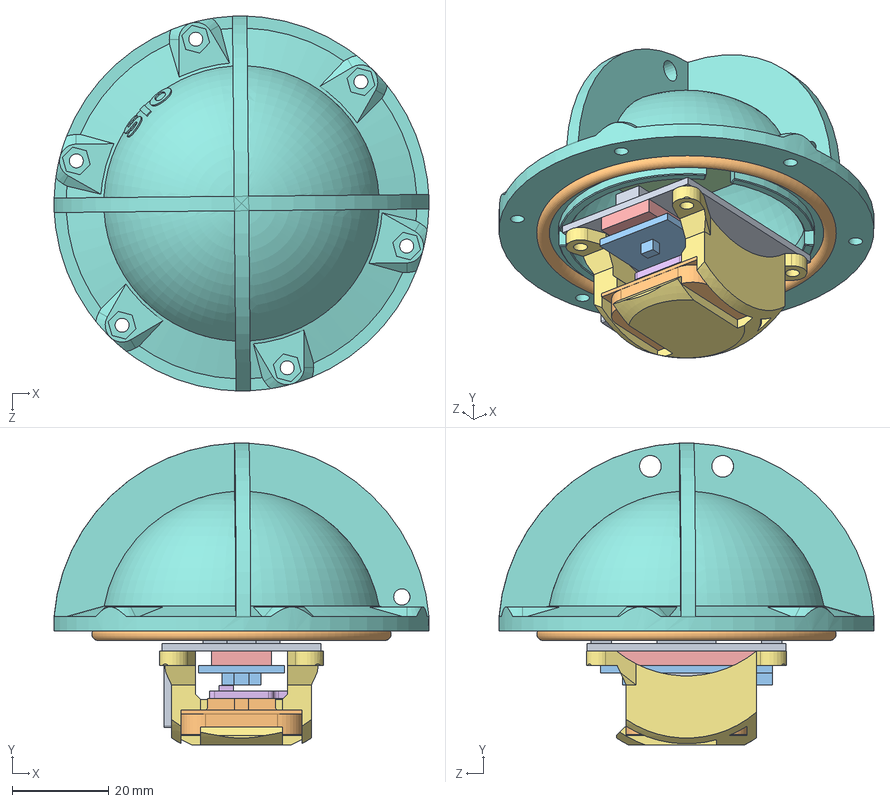
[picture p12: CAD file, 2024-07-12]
Drifter2_Assem1.SLDASM
77.7 x 62.6 x 77.7 mm
Sparkfun_NEO-M8P
TAOGLAS_AGPP25F
Teensy_3-2
Battery_AllSizes_configurations
internalmounts
Pimoroni_ICM20948
GPSmount
housing2_rev2
Sparkfun_RFM69HCW_transceiver
2418T159_Oil-Resistant Soft Buna-N O-Rings

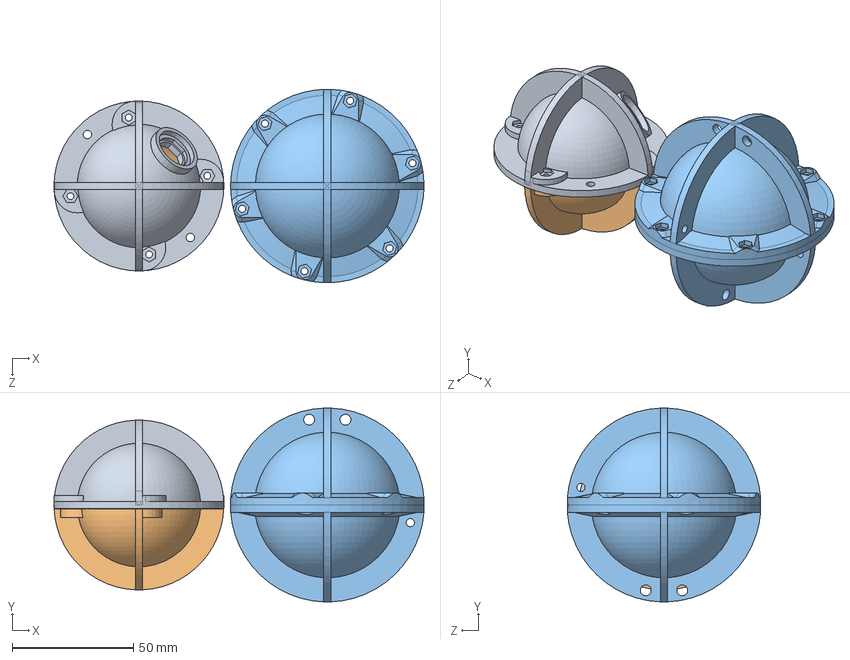
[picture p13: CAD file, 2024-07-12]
Housing_comparison.SLDASM
152.5 x 79.9 x 79.7 mm
enclosure_half_one
enclosure_half_two
housing2_rev2 x 2

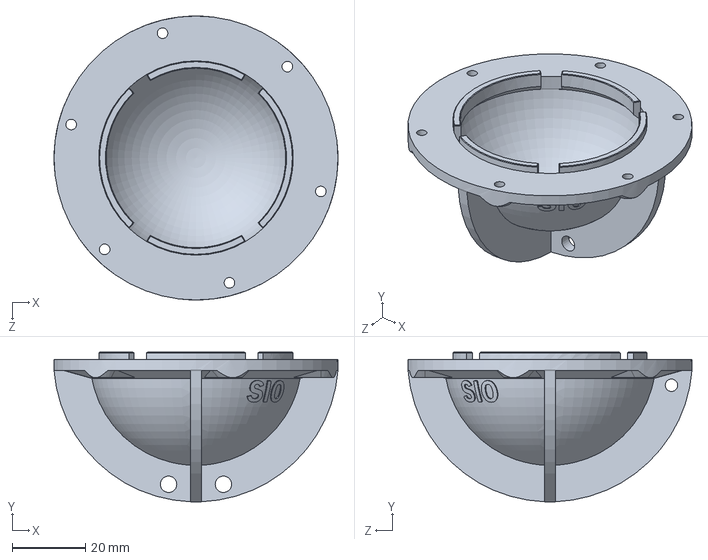
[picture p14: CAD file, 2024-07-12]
HousingMounts.SLDASM
77.7 x 41.0 x 77.7 mm

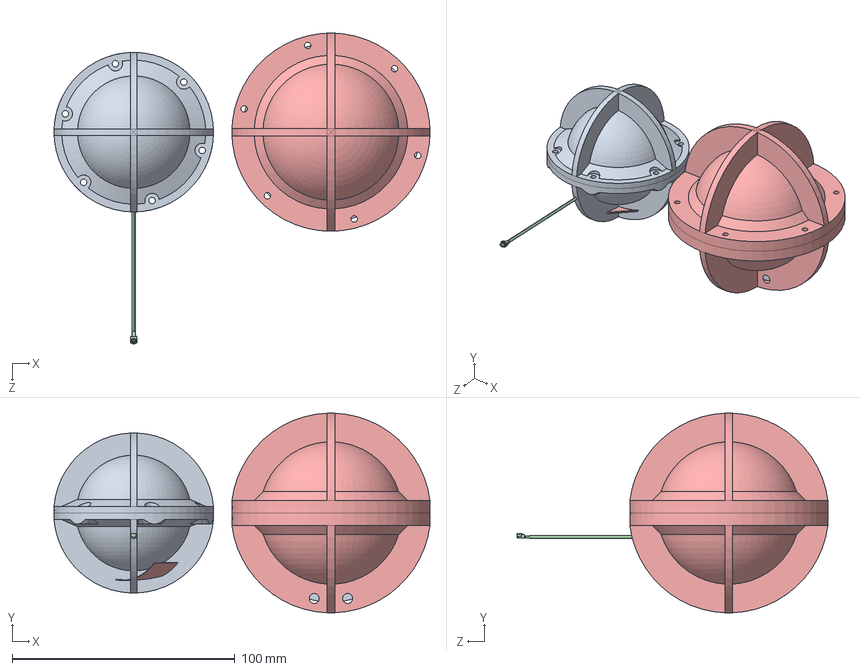
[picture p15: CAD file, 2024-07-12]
Drifter2_COMPARISON.SLDASM
168.9 x 89.7 x 139.6 mm
Teensy_3-2 x 2
Battery_AllSizes_configurations x 3
internalmounts x 2
Pimoroni_ICM20948 x 2
housing2_rev2 x 4
Sparkfun_RFM69HCW_transceiver x 2
GNSSOEM_ZEDF9P_ELT0128
2jm3201c2f.step
Sparkfun_NEO-M8P
TAOGLAS_AGPP25F
GPSmount
2418T183_Oil-Resistant Soft Buna-N O-Rings

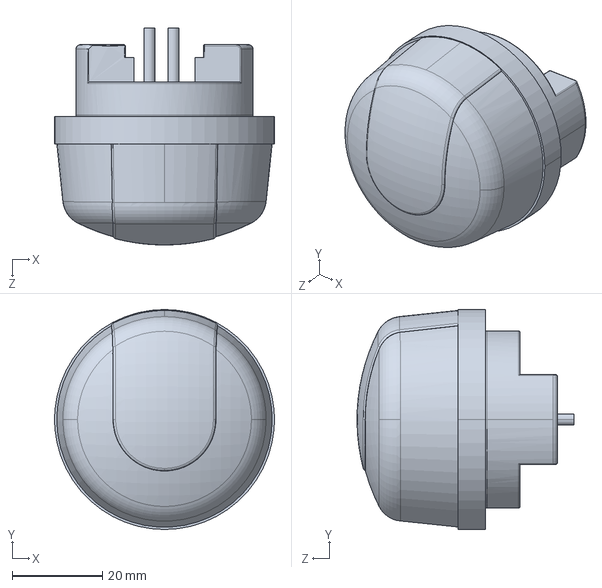
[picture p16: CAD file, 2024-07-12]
MA104.C.AB.015_AXIS.SLDASM
48.8 x 48.8 x 48.1 mm

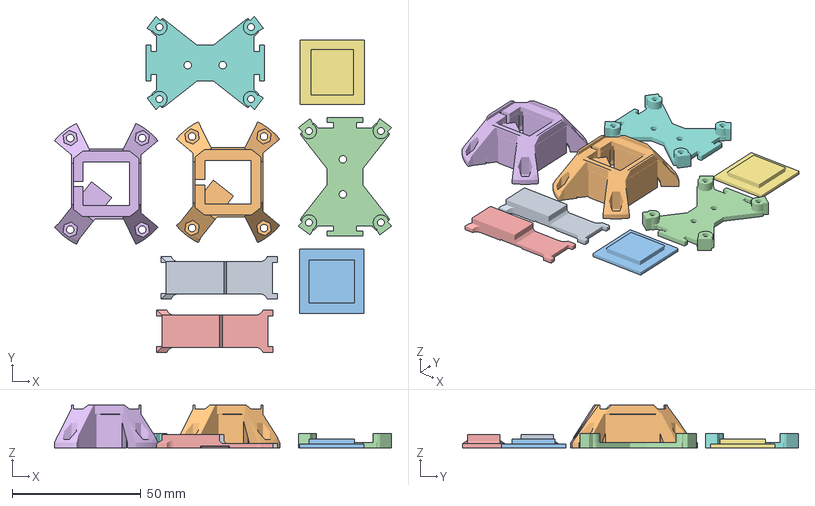
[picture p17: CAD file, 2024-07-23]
3DPrinting/Drifter2-1_InternalMounts.3mf
130.9 x 130.5 x 16.5 mm
20240718_internalmounts5-1-SUPPORTS.STL
20240718_InternalMounts5-1_GPS_Cradle-SUPPORTS.STL
20240718_internalmounts5_GPS_minicradle.STL
20240718_Internalmount5_housingmount.STL
20240718_internalmounts5-1-SUPPORTS.STL(1)
20240718_InternalMounts5-1_GPS_Cradle-SUPPORTS.STL(1)
20240718_internalmounts5_GPS_minicradle.STL(1)
20240718_Internalmount5_housingmount.STL(1)

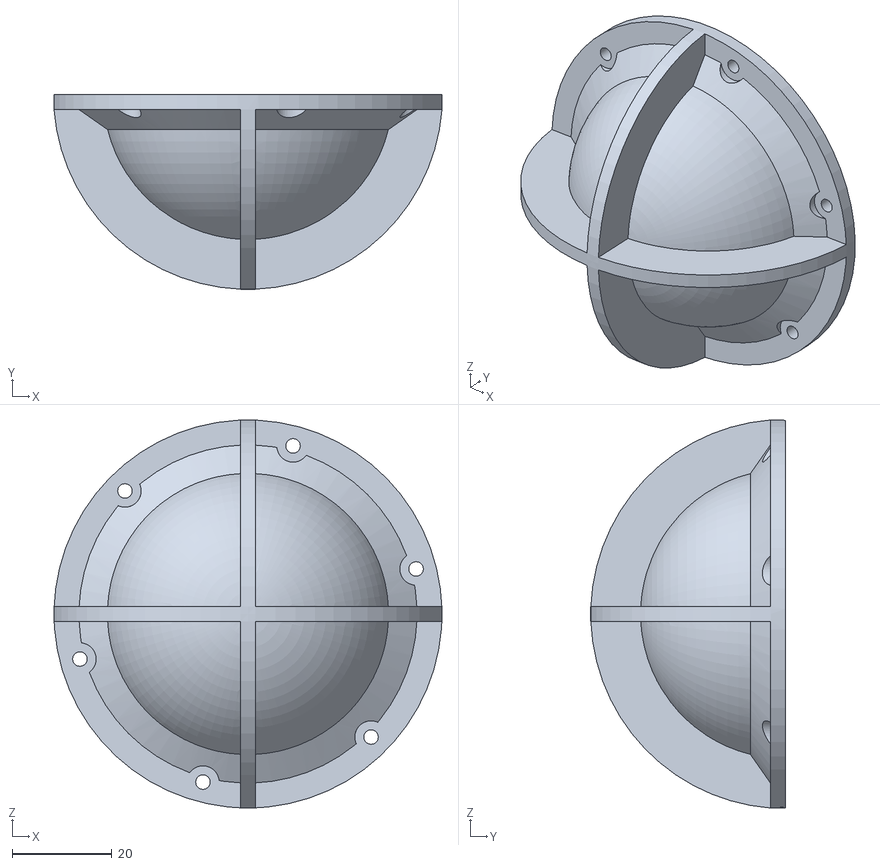
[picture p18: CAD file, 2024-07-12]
Renders/housing2_rev2_20240223.STL
77.7 x 39.0 x 77.7

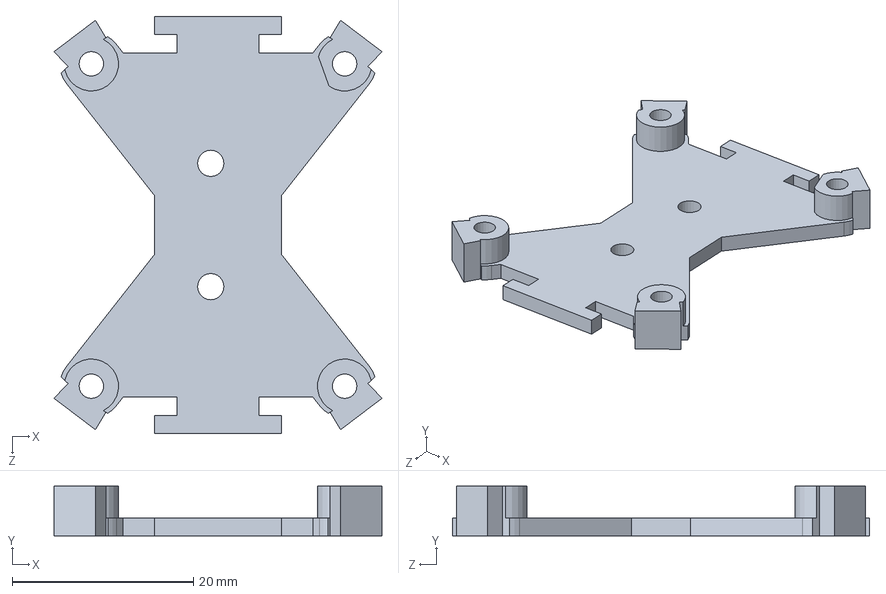
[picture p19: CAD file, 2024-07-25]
Internalmount5_housingmount.SLDPRT
36.2 x 5.50 x 46.0 mm

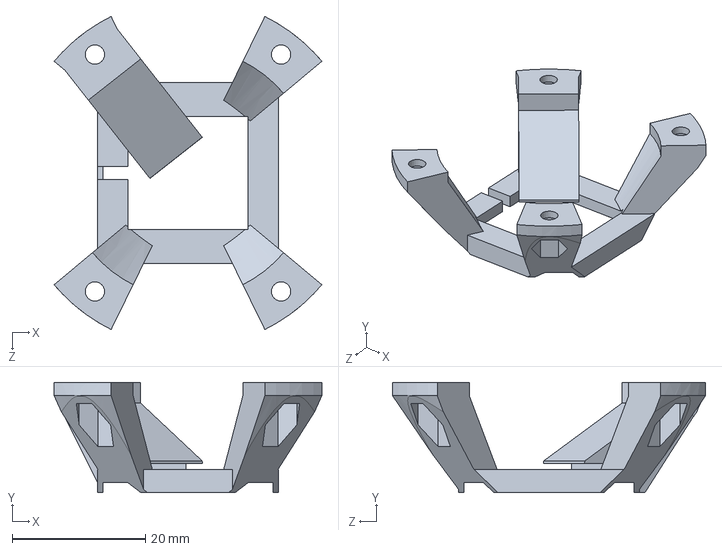
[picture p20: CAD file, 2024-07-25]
InternalMounts5_GPS_Cradle.SLDPRT
40.2 x 16.5 x 47.0 mm

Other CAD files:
Drifter2_Assem_GSM2.SLDASM
1W-LED_280mA_Xiaoyztan.SLDPRT
internalmounts5_GPS_minicradle.SLDPRT
internalmounts.SLDPRT
18650 bat.SLDPRT
2418T159_Oil-Resistant Soft Buna-N O-Rings.SLDPRT
2418T183_Oil-Resistant Soft Buna-N O-Rings.SLDPRT
2418T185_Oil-Resistant Soft Buna-N O-Rings.SLDPRT
2jm3201c2f.step
92290A060_Super-Corrosion-Resistant 316 Stainless Steel Socket Head Screw.SLDPRT
94205A101_316 Stainless Steel Nylon-Insert Locknut.SLDPRT
BALL.SLDPRT
Battery_1100mAH.SLDPRT
Battery_AllSizes_configurations.SLDPRT
EXVIST_4GLTEGSM_EC25-AFX.SLDPRT
FINAL/20240412_housing2_rev2_2-140.STL
FINAL/20240412_housing2_rev2_2-140_UP.STL
FINAL/20240424_housing2_rev2_2-140.STL
FINAL/20240424_housing2_rev2_2-140_UP.STL
FINAL/20240425_housing2_rev2_2-140.STL
FINAL/20240425_housing2_rev2_2-140_UP.STL
FINAL/20240502_GPSmount3.STL
FINAL/20240503_Internalmount3.STL
FINAL/20240503_Internalmount3_SOLID.STL
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

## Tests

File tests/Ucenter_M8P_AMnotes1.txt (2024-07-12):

PACKETS
17:24:18  R -> UBX 03-09,  Size 208,  'Unknown'
17:24:18  R -> UBX SEC,  Size 908,  'Security'
17:24:18  R -> UBX RXM-RAWX,  Size 216,  'Multi-GNSS Raw Measurement Data'
17:24:18  R -> UBX MON,  Size 436,  'Monitor'
17:24:18  R -> UBX MON-MSGPP,  Size 128,  'MSGPP Message Parse & Process'
17:24:18  R -> UBX MON-IO,  Size 128,  'IO System'
17:24:18  R -> UBX MON,  Size 1060,  'Monitor'
17:24:18  R -> UBX NAV-SOL,  Size  60,  'Navigation Solution'
17:24:19  R -> UBX NAV-PVT,  Size 100,  'Navigation PVT Solution'
17:24:19  R -> UBX NAV-SVINFO,  Size 208,  'Satellite Status and Information'
17:24:19  R -> UBX NAV-ORB,  Size 292,  'Orbit Availability Info'
17:24:19  R -> UBX NAV-SAT,  Size 208,  'Satellite Status and Information'
17:24:19  R -> UBX NAV-CLOCK,  Size  28,  'Clock Status'
17:24:19  R -> UBX NAV-SVIN,  Size  48,  'Survey-in'
17:24:19  R -> UBX NAV-RELPOSNED,  Size  48,  'Relative Position NED'
17:24:19  R -> NMEA GNGGA,  Size  75,  'Global Positioning System Fix Data'
17:24:19  R -> UBX 0C-31,  Size 776,  'Unknown'
17:24:19  R -> UBX 0C-34,  Size 120,  'Unknown'
17:24:19  R -> UBX 0C-43,  Size  16,  'Unknown'
17:24:19  R -> UBX 0C-10,  Size 748,  'Unknown'
17:24:19  R -> UBX 03-09,  Size 208,  'Unknown'
17:24:19  R -> UBX SEC,  Size 1020,  'Security'
17:24:19  R -> UBX RXM-RAWX,  Size 216,  'Multi-GNSS Raw Measurement Data'
17:24:19  R -> UBX MON,  Size 436,  'Monitor'
17:24:19  R -> UBX MON-MSGPP,  Size 128,  'MSGPP Message Parse & Process'
17:24:19  R -> UBX MON-IO,  Size 128,  'IO System'
17:24:19  R -> UBX MON,  Size 1060,  'Monitor'
17:24:19  R -> UBX NAV-SOL,  Size  60,  'Navigation Solution'
17:24:20  R -> UBX NAV-PVT,  Size 100,  'Navigation PVT Solution'
17:24:20  R -> UBX NAV-SVINFO,  Size 208,  'Satellite Status and Information'
17:24:20  R -> UBX NAV-ORB,  Size 292,  'Orbit Availability Info'
17:24:20  R -> UBX NAV-SAT,  Size 208,  'Satellite Status and Information'
17:24:20  R -> UBX NAV-CLOCK,  Size  28,  'Clock Status'
17:24:20  R -> UBX NAV-SVIN,  Size  48,  'Survey-in'
17:24:20  R -> UBX NAV-RELPOSNED,  Size  48,  'Relative Position NED'
17:24:20  R -> NMEA GNGGA,  Size  75,  'Global Positioning System Fix Data'
17:24:20  R -> UBX 0C-31,  Size 776,  'Unknown'
17:24:20  R -> UBX 0C-34,  Size 120,  'Unknown'
17:24:20  R -> UBX 0C-43,  Size  16,  'Unknown'
17:24:20  R -> UBX 0C-10,  Size 748,  'Unknown'
17:24:20  R -> UBX 03-09,  Size 208,  'Unknown'
17:24:20  R -> UBX SEC,  Size 1020,  'Security'
17:24:20  R -> UBX RXM-RAWX,  Size 184,  'Multi-GNSS Raw Measurement Data'
17:24:20  R -> UBX MON,  Size 436,  'Monitor'
17:24:20  R -> UBX MON-MSGPP,  Size 128,  'MSGPP Message Parse & Process'
17:24:20  R -> UBX MON-IO,  Size 128,  'IO System'
17:24:20  R -> UBX MON,  Size 1060,  'Monitor'
17:24:20  R -> UBX NAV-SOL,  Size  60,  'Navigation Solution'
17:24:21  R -> UBX NAV-PVT,  Size 100,  'Navigation PVT Solution'
17:24:21  R -> UBX NAV-SVINFO,  Size 208,  'Satellite Status and Information'
17:24:21  R -> UBX NAV-ORB,  Size 292,  'Orbit Availability Info'
17:24:21  R -> UBX NAV-SAT,  Size 208,  'Satellite Status and Information'
17:24:21  R -> UBX NAV-CLOCK,  Size  28,  'Clock Status'
17:24:21  R -> UBX NAV-SVIN,  Size  48,  'Survey-in'
17:24:21  R -> UBX NAV-RELPOSNED,  Size  48,  'Relative Position NED'
17:24:21  R -> NMEA GNGGA,  Size  75,  'Global Positioning System Fix Data'
17:24:21  R -> UBX 0C-31,  Size 776,  'Unknown'
17:24:21  R -> UBX 0C-34,  Size 120,  'Unknown'
17:24:21  R -> UBX 0C-43,  Size  16,  'Unknown'
17:24:21  R -> UBX 0C-10,  Size 748,  'Unknown'
17:24:21  R -> UBX 03-09,  Size 208,  'Unknown'
17:24:21  R -> UBX SEC,  Size 1020,  'Security'
17:24:21  R -> UBX RXM-RAWX,  Size 184,  'Multi-GNSS Raw Measurement Data'
17:24:21  R -> UBX MON,  Size 436,  'Monitor'
17:24:21  R -> UBX MON-MSGPP,  Size 128,  'MSGPP Message Parse & Process'
17:24:21  R -> UBX MON-IO,  Size 128,  'IO System'
17:24:21  R -> UBX MON,  Size 1060,  'Monitor'
17:24:21  R -> UBX NAV-SOL,  Size  60,  'Navigation Solution'
17:24:22  R -> UBX NAV-PVT,  Size 100,  'Navigation PVT Solution'
17:24:22  R -> UBX NAV-SVINFO,  Size 208,  'Satellite Status and Information'
17:24:22  R -> UBX NAV-ORB,  Size 292,  'Orbit Availability Info'
17:24:22  R -> UBX NAV-SAT,  Size 208,  'Satellite Status and Information'
17:24:22  R -> UBX NAV-CLOCK,  Size  28,  'Clock Status'
17:24:22  R -> UBX NAV-SVIN,  Size  48,  'Survey-in'
17:24:22  R -> UBX NAV-RELPOSNED,  Size  48,  'Relative Position NED'
17:24:22  R -> NMEA GNGGA,  Size  75,  'Global Positioning System Fix Data'
17:24:22  R -> UBX 0C-31,  Size 776,  'Unknown'
17:24:22  R -> UBX 0C-34,  Size 120,  'Unknown'
17:24:22  R -> UBX 0C-43,  Size  16,  'Unknown'
17:24:22  R -> UBX 0C-10,  Size 748,  'Unknown'
17:24:22  R -> UBX 03-09,  Size 208,  'Unknown'
17:24:22  R -> UBX SEC,  Size 1020,  'Security'
17:24:22  R -> UBX RXM-RAWX,  Size 184,  'Multi-GNSS Raw Measurement Data'
17:24:22  R -> UBX MON,  Size 436,  'Monitor'
17:24:22  R -> UBX MON-MSGPP,  Size 128,  'MSGPP Message Parse & Process'
17:24:22  R -> UBX MON-IO,  Size 128,  'IO System'
17:24:22  R -> UBX MON,  Size 1060,  'Monitor'
17:24:22  R -> UBX NAV-SOL,  Size  60,  'Navigation Solution'
17:24:23  R -> UBX NAV-PVT,  Size 100,  'Navigation PVT Solution'
17:24:23  R -> UBX NAV-SVINFO,  Size 208,  'Satellite Status and Information'
17:24:23  R -> UBX NAV-ORB,  Size 292,  'Orbit Availability Info'
17:24:23  R -> UBX NAV-SAT,  Size 208,  'Satellite Status and Information'
17:24:23  R -> UBX NAV-CLOCK,  Size  28,  'Clock Status'
17:24:23  R -> UBX NAV-SVIN,  Size  48,  'Survey-in'
17:24:23  R -> UBX NAV-RELPOSNED,  Size  48,  'Relative Position NED'
17:24:23  R -> NMEA GNGGA,  Size  75,  'Global Positioning System Fix Data'
17:24:23  R -> UBX 0C-31,  Size 776,  'Unknown'
17:24:23  R -> UBX 0C-34,  Size 120,  'Unknown'
17:24:23  R -> UBX 0C-43,  Size  16,  'Unknown'
17:24:23  R -> UBX 0C-10,  Size 748,  'Unknown'
17:24:23  R -> UBX 03-09,  Size 208,  'Unknown'
17:24:23  R -> UBX SEC,  Size 1020,  'Security'
17:24:23  R -> UBX RXM-RAWX,  Size 216,  'Multi-GNSS Raw Measurement Data'
17:24:23  R -> UBX MON,  Size 436,  'Monitor'
17:24:23  R -> UBX MON-MSGPP,  Size 128,  'MSGPP Message Parse & Process'
17:24:23  R -> UBX MON-IO,  Size 128,  'IO System'
17:24:23  R -> UBX MON,  Size 1060,  'Monitor'
17:24:23  R -> UBX NAV-SOL,  Size  60,  'Navigation Solution'
17:24:24  R -> UBX NAV-PVT,  Size 100,  'Navigation PVT Solution'
17:24:24  R -> UBX NAV-SVINFO,  Size 208,  'Satellite Status and Information'
17:24:24  R -> UBX NAV-ORB,  Size 292,  'Orbit Availability Info'
17:24:24  R -> UBX NAV-SAT,  Size 208,  'Satellite Status and Information'
17:24:24  R -> UBX NAV-CLOCK,  Size  28,  'Clock Status'
17:24:24  R -> UBX NAV-SVIN,  Size  48,  'Survey-in'
17:24:24  R -> UBX NAV-RELPOSNED,  Size  48,  'Relative Position NED'
17:24:24  R -> NMEA GNGGA,  Size  75,  'Global Positioning System Fix Data'
17:24:24  R -> UBX 0C-31,  Size 776,  'Unknown'
17:24:24  R -> UBX 0C-34,  Size 120,  'Unknown'
17:24:24  R -> UBX 0C-43,  Size  16,  'Unknown'
17:24:24  R -> UBX 0C-10,  Size 748,  'Unknown'
17:24:24  R -> UBX SEC,  Size  76,  'Security'
17:24:24  R -> UBX SEC,  Size  76,  'Security'
17:24:24  R -> UBX SEC,  Size  76,  'Security'
17:24:24  R -> UBX SEC,  Size  76,  'Security'
17:24:24  R -> UBX SEC,  Size  76,  'Security'
17:24:24  R -> UBX 03-09,  Size 208,  'Unknown'
17:24:24  R -> UBX SEC,  Size 1020,  'Security'
17:24:24  R -> UBX RXM-RAWX,  Size 216,  'Multi-GNSS Raw Measurement Data'
17:24:24  R -> UBX MON,  Size 436,  'Monitor'
17:24:24  R -> UBX MON-MSGPP,  Size 128,  'MSGPP Message Parse & Process'
17:24:24  R -> UBX MON-IO,  Size 128,  'IO System'
17:24:24  R -> UBX MON,  Size 1060,  'Monitor'
17:24:24  R -> UBX NAV-SOL,  Size  60,  'Navigation Solution'
17:24:25  R -> UBX NAV-PVT,  Size 100,  'Navigation PVT Solution'
17:24:25  R -> UBX NAV-SVINFO,  Size 208,  'Satellite Status and Information'
17:24:25  R -> UBX NAV-ORB,  Size 292,  'Orbit Availability Info'
17:24:25  R -> UBX NAV-SAT,  Size 208,  'Satellite Status and Information'
17:24:25  R -> UBX NAV-CLOCK,  Size  28,  'Clock Status'
17:24:25  R -> UBX NAV-SVIN,  Size  48,  'Survey-in'
17:24:25  R -> UBX NAV-RELPOSNED,  Size  48,  'Relative Position NED'
17:24:25  R -> NMEA GNGGA,  Size  75,  'Global Positioning System Fix Data'
17:24:25  R -> UBX 0C-31,  Size 776,  'Unknown'
17:24:25  R -> UBX 0C-34,  Size 120,  'Unknown'
17:24:25  R -> UBX 0C-43,  Size  16,  'Unknown'
17:24:25  R -> UBX 0C-10,  Size 748,  'Unknown'
17:24:25  R -> UBX 03-09,  Size 208,  'Unknown'
17:24:25  R -> UBX SEC,  Size 1020,  'Security'
17:24:25  R -> UBX RXM-RAWX,  Size 216,  'Multi-GNSS Raw Measurement Data'
17:24:25  R -> UBX MON,  Size 436,  'Monitor'
17:24:25  R -> UBX MON-MSGPP,  Size 128,  'MSGPP Message Parse & Process'
17:24:25  R -> UBX MON-IO,  Size 128,  'IO System'
17:24:25  R -> UBX MON,  Size 1060,  'Monitor'
17:24:25  R -> UBX NAV-SOL,  Size  60,  'Navigation Solution'
17:24:26  R -> UBX NAV-PVT,  Size 100,  'Navigation PVT Solution'
17:24:26  R -> UBX NAV-SVINFO,  Size 208,  'Satellite Status and Information'
17:24:26  R -> UBX NAV-ORB,  Size 292,  'Orbit Availability Info'
17:24:26  R -> UBX NAV-SAT,  Size 208,  'Satellite Status and Information'
17:24:26  R -> UBX NAV-CLOCK,  Size  28,  'Clock Status'
17:24:26  R -> UBX NAV-SVIN,  Size  48,  'Survey-in'
17:24:26  R -> UBX NAV-RELPOSNED,  Size  48,  'Relative Position NED'
17:24:26  R -> NMEA GNGGA,  Size  75,  'Global Positioning System Fix Data'
17:24:26  R -> UBX 0C-31,  Size 776,  'Unknown'
17:24:26  R -> UBX 0C-34,  Size 120,  'Unknown'
17:24:26  R -> UBX 0C-43,  Size  16,  'Unknown'
17:24:26  R -> UBX 0C-10,  Size 748,  'Unknown'
17:24:26  R -> UBX 03-09,  Size 208,  'Unknown'
17:24:26  R -> UBX SEC,  Size 972,  'Security'
17:24:26  R -> UBX RXM-RAWX,  Size 216,  'Multi-GNSS Raw Measurement Data'
17:24:26  R -> UBX MON,  Size 436,  'Monitor'
17:24:26  R -> UBX MON-MSGPP,  Size 128,  'MSGPP Message Parse & Process'
17:24:26  R -> UBX MON-IO,  Size 128,  'IO System'
17:24:26  R -> UBX MON,  Size 1060,  'Monitor'
17:24:26  R -> UBX NAV-SOL,  Size  60,  'Navigation Solution'
17:24:27  R -> UBX NAV-PVT,  Size 100,  'Navigation PVT Solution'
17:24:27  R -> UBX NAV-SVINFO,  Size 208,  'Satellite Status and Information'
17:24:27  R -> UBX NAV-ORB,  Size 292,  'Orbit Availability Info'
17:24:27  R -> UBX NAV-SAT,  Size 208,  'Satellite Status and Information'
17:24:27  R -> UBX NAV-CLOCK,  Size  28,  'Clock Status'
17:24:27  R -> UBX NAV-SVIN,  Size  48,  'Survey-in'
17:24:27  R -> UBX NAV-RELPOSNED,  Size  48,  'Relative Position NED'
17:24:27  R -> NMEA GNGGA,  Size  75,  'Global Positioning System Fix Data'
17:24:27  R -> UBX 0C-31,  Size 776,  'Unknown'
17:24:27  R -> UBX 0C-34,  Size 120,  'Unknown'
17:24:27  R -> UBX 0C-43,  Size  16,  'Unknown'
17:24:27  R -> UBX 0C-10,  Size 748,  'Unknown'

BINARY DATA
17:35:13  0000  B5 62 27 00 F4 03 02 00 F0 03 83 C6 78 A6 67 FD  µb'.ô...ð..Æx¦gý
          0010  3C D0 D8 59 A4 7F 55 26 27 18 03 19 DD A1 32 91  <ÐØY¤.U&'...Ý¡2.
          0020  DC D7 84 E5 20 A5 70 45 C7 7E 9C 46 25 5E CE 2E  Ü×.å ¥pEÇ~.F%^Î.
          0030  DD 2F 25 79 A2 8A A8 0A 08 85 A8 46 DA DF 31 E1  Ý/%y¢.¨...¨FÚß1á
          0040  BC AE 6E 59 A4 6E 07 8A 06 05 E3 46 DA A1 31 91  ¼®nY¤n....ãFÚ¡1.
          0050  2E D0 D8 40 EE EB 57 8A F7 05 83 46 DA A1 31 71  .ÐØ@îëW.÷..FÚ¡1q
          0060  3C D0 D1 59 A4 EB 57 8A F7 05 83 46 DA A1 31 91  <ÐÑY¤ëW.÷..FÚ¡1.
          0070  30 D0 D8 59 A4 75 57 8A F7 05 A3 47 DB AB 91 50  0ÐØY¤uW.÷.£GÛ«.P
          0080  3C 84 78 59 A6 75 76 8A F7 05 69 4A DA 5E 31 91  <.xY¦uv.÷.iJÚ^1.
          0090  F6 25 D8 DB D5 14 D7 8A 08 05 83 B9 DA A1 31 91  ö%ØÛÕ.×....¹Ú¡1.
          00A0  22 D0 D2 85 A4 75 57 75 F7 3A 83 C3 DA A1 31 91  "ÐÒ.¤uWu÷:.ÃÚ¡1.
          00B0  3D D0 D8 D9 24 77 57 5F F7 1A 43 C6 5C A1 76 E1  =ÐØÙ$wW_÷.CÆ\¡vá
          00C0  58 27 DC DF 60 83 48 72 38 32 F5 C6 23 91 9B 05  X'Üß`.Hr82õÆ#...
          00D0  F4 0E 13 51 EA F7 B2 04 49 DD A3 47 CF A1 31 51  ô..Qê÷².IÝ£GÏ¡1Q
          00E0  3C D0 08 59 E4 75 57 8B C1 85 F3 C6 D8 87 31 91  <Ð.YäuW.Á.óÆØ.1.
          00F0  BA AF 58 6A A0 A3 10 77 F7 F8 A8 CA BE A3 2E 51  º¯Xj £.w÷ø¨Ê¾£.Q
          0100  85 CA A2 76 6F AF 0F AC EE 86 A3 46 55 A1 E6 9F  .Ê¢vo¯.¬î.£FU¡æ.
          0110  6A D9 80 6B 7A 37 57 8A A4 05 83 C4 DA A5 31 B1  jÙ.kz7W.¤..ÄÚ¥1±
          0120  3C D0 98 D9 64 73 57 0B F5 1A 83 46 50 A0 76 E0  <Ð.ÙdsW.õ..FP và
          0130  3E D1 FC DF 8E 83 D7 C0 39 23 DB B9 43 91 57 B9  >Ñüß..×À9#Û¹C.W¹
          0140  CF 74 12 86 EB BD 7F B7 49 9F 63 59 A4 5F CE CE  Ït..ë½.·I.cY¤_ÎÎ
          0150  38 D0 76 5E 9B 74 57 88 89 85 F3 C6 DB B5 31 91  8Ðv^.tW...óÆÛµ1.
          0160  BA AF B8 2A 80 23 90 77 F7 CC BF CA B9 A3 23 F1  º¯¸*.#.w÷Ì¿Ê¹£#ñ
          0170  C5 3B 5A 76 6F B1 8A D3 EE EF 9C 39 8E 5E E7 F4  Å;Zvo±.Óîï.9.^çô
          0180  84 ED 85 89 33 F4 A8 8A 3C 05 42 44 DA A7 31 F1  .í..3ô¨.<.BDÚ§1ñ
          0190  3E D0 98 59 64 7F 97 8A F5 10 83 39 DA A5 10 B1  >Ð.Yd...õ..9Ú¥.±
          01A0  3C D0 DA A6 A4 75 57 96 F7 AC 83 46 70 93 39 AC  <ÐÚ¦¤uW.÷¬.Fp.9¬
          01B0  3C D0 A8 59 A4 75 57 8A FF 05 83 46 CC 5F 31 91  <Ð¨Y¤uW.ÿ..FÌ_1.
          01C0  3C 2F D8 59 A4 8A 57 89 75 05 F3 C6 D9 91 31 91  </ØY¤.W.u.óÆÙ.1.
          01D0  BA AF F8 6A A0 23 10 77 F7 F8 CE CA BE A3 2E 91  º¯øj #.w÷øÎÊ¾£..
          01E0  45 76 EC 76 6F 57 0E 7D EE F4 C3 46 50 A1 E1 E1  EvìvoW.}îôÃFP¡áá
          01F0  43 62 0E 1B 9F D5 57 8A 91 85 42 46 DA A7 31 D1  Cb...ÕW...BFÚ§1Ñ
          0200  3D D0 98 59 64 7B 37 8A F5 10 83 39 DA A5 10 B1  =Ð.Yd{7.õ..9Ú¥.±
          0210  3C D0 DA A6 A4 75 57 6A F7 A1 83 46 70 93 02 89  <ÐÚ¦¤uWj÷¡.Fp...
          0220  3C D0 A9 59 A4 75 57 8A FF 05 83 46 C4 A0 31 91  <Ð©Y¤uW.ÿ..FÄ 1.
          0230  3C 2F D8 59 A4 8B 57 8E 57 05 C3 46 DA A9 31 91  </ØY¤.W.W.ÃFÚ©1.
          0240  3C 84 78 59 A6 75 76 8A F7 05 1B 4A DA 5E 31 91  <.xY¦uv.÷..JÚ^1.
          0250  C5 E8 D8 76 6E 74 D0 8A 08 85 83 C6 5A A1 31 91  ÅèØvntÐ....ÆZ¡1.
          0260  2C D0 D8 33 A4 75 57 75 F7 BA 43 C3 DA A1 31 91  ,ÐØ3¤uWu÷ºCÃÚ¡1.
          0270  3E D0 D8 59 44 67 F7 0B F7 10 03 C2 D0 A4 74 E0  >ÐØYDg÷.÷..ÂÐ¤tà
          0280  3D D1 FC DF 58 83 D7 41 F5 42 2E 39 90 93 28 1F  =ÑüßX.×AõB.9..(.
          0290  D7 A3 A9 AC D4 71 CD 67 FF 3E 60 6C 7C 5E CE 4E  ×£©¬ÔqÍgÿ>`l|^ÎN
          02A0  39 F9 CC D3 7B 34 B7 8F C3 85 F2 C6 D9 99 31 91  9ùÌÓ{4·.Ã.òÆÙ.1.
          02B0  B6 AE 78 2A 80 73 10 F7 F7 85 B0 4A D8 A3 31 F1  ¶®x*.s.÷÷.°JØ£1ñ
          02C0  A5 F1 86 76 6E 8B 71 6F EF FD 83 46 51 A1 E8 4E  ¥ñ.vn.qoïý.FQ¡èN
          02D0  50 BB 3F 13 5F B1 57 8A D2 05 43 40 D8 CD D1 71  P»?._±W.Ò.C@ØÍÑq
          02E0  3C D0 07 59 44 63 F7 8A E3 10 83 39 DA A5 10 B1  <Ð.YDc÷.ã..9Ú¥.±
          02F0  3C D0 DA A6 A4 75 57 D2 F7 99 83 46 F0 93 03 8F  <ÐÚ¦¤uWÒ÷..Fð...
          0300  23 D0 A8 59 52 75 57 8A FF 05 83 46 C0 A1 31 91  #Ð¨YRuW.ÿ..FÀ¡1.
          0310  3C 2F D8 59 A4 8B 57 8C 6F 05 A3 47 DB BB D1 51  </ØY¤.W.o.£GÛ»ÑQ
          0320  3C 84 D8 59 A6 75 76 8A F7 05 97 4A DA 5E 31 91  <.ØY¦uv.÷..JÚ^1.
          0330  F6 29 D8 DB D4 E4 EA 8A 09 05 83 C6 DA A1 31 91  ö)ØÛÔäê....ÆÚ¡1.
          0340  3A D0 D8 39 A4 75 57 75 F7 BA 83 4D DA A1 31 91  :ÐØ9¤uWu÷º.MÚ¡1.
          0350  3F D0 D8 D9 A4 6F 57 8B F7 10 03 C6 D0 A0 74 E0  ?ÐØÙ¤oW.÷..ÆÐ tà
          0360  3E D1 FC DF 88 D1 57 47 F7 10 32 B9 C3 91 C4 48  >Ñüß.ÑWG÷.2¹Ã.ÄH
          0370  DF 9C 11 A6 B7 C1 26 74 48 4D 63 5D A1 5F CE AE  ß..¦·Á&tHMc]¡_Î®
          0380  3E D8 A1 5C 7B 34 37 8D 6B 05 A3 46 D8 85 31 91  >Ø¡\{47.k.£FØ.1.
          0390  3C 84 B8 59 A6 75 76 8A F7 05 53 4A DA 5E 31 91  <.¸Y¦uv.÷.SJÚ^1.
          03A0  85 8B D8 76 6D 94 6E 8A 09 85 83 B9 C5 A1 31 91  ..Øvm.n....¹Å¡1.
          03B0  30 D0 2E EE A4 75 57 75 F7 BA 83 4B DA A1 31 91  0Ð.î¤uWu÷º.KÚ¡1.
          03C0  3F D0 D8 D9 24 6B 57 8B F7 10 E3 C6 D0 A0 74 E0  ?ÐØÙ$kW.÷.ãÆÐ tà
          03D0  3D D1 FC DF 66 2F 57 9C F7 44 94 C6 C3 91 80 1F  =Ñüßf/W.÷D.ÆÃ...
          03E0  8A 8B 11 59 6D 73 62 ED 49 77 63 5D 88 A1 31 71  ...YmsbíIwc].¡1q
          03F0  3E D8 37 5C 7B 35 77 B1 11 7C 54 7E              >Ø7\{5w±.|T~.
          
17:35:13  0000  B5 62 02 15 D0 00 75 93 18 04 90 F5 18 41 0C 09  µb..Ð.u....õ.A..
          0010  12 06 01 01 59 3B FF 5F 5B 76 84 66 74 41 43 46  ....Y;ÿ_[v.ftACF
          0020  23 81 20 CD 9A 41 30 74 DD 43 00 0C 00 00 F4 FB  #. Í.A0tÝC....ôû
          0030  26 06 01 08 07 00 0A DA E6 6D 69 57 75 41 E7 0F  &......ÚæmiWuAç.
          0040  25 34 9A 09 9C 41 E2 6D C9 44 00 14 00 00 F4 FB  %4...AâmÉD....ôû
          0050  24 06 01 08 0F 00 A6 B3 51 97 AE A7 77 41 B6 E2  $.....¦³Q.®§wA¶â
          0060  FA B4 B4 13 9F 41 8E 0A 40 C5 00 06 00 00 00 00  ú´´..A..@Å......
          0070  11 0B 0F 0C 01 00 04 5C FA 7D 56 2F 75 41 AD 34  .......\ú}V/uA­4
          0080  45 BB F4 D4 9B 41 90 76 BE C4 00 0B 00 00 58 2F  E»ôÔ.A.v¾Ä....X/
          0090  1C 07 03 08 07 00 33 83 1B 8B A3 09 75 41 70 EC  ......3...£.uApì
          00A0  E5 F1 6D A3 9B 41 DA F9 05 45 00 19 00 00 F4 FB  åñm£.AÚù.E....ôû
          00B0  22 07 02 08 07 00 9C 43 F9 2F 18 8F 77 41 39 CC  "......Cù/..wA9Ì
          00C0  04 60 67 F3 9E 41 D8 67 14 45 00 1D 00 00 00 00  .`gó.AØg.E......
          00D0  13 0B 0F 0C 01 00 B5 28                          ......µ(.
          
17:35:13  0000  B5 62 0A 11 AC 01 01 01 5A 89 10 00 98 02 00 00  µb..¬...Z.......
          0010  CE 00 00 00 BB 05 00 00 00 00 00 02 1F 37 46 00  Î...»........7F.
          0020  00 00 00 00 00 01 CE BB 07 00 00 9D 03 A3 76 16  ......Î».....£v.
          0030  00 18 FB 00 20 00 01 40 00 78 3E 87 BF 69 64 6C  ..û. ..@.x>.¿idl
          0040  00 01 00 00 86 05 00 00 00 00 DC 34 02 20 23 00  ..........Ü4. #.
          0050  00 00 00 00 00 00 CC 08 00 00 58 FC 00 20 10 09  ......Ì...Xü. ..
          0060  60 03 40 00 00 00 69 6F 00 00 02 00 00 01 05 00  `.@...io........
          0070  00 00 00 00 00 00 00 00 00 00 00 00 00 00 00 F8  ...............ø
          0080  04 00 00 A8 05 01 20 38 04 28 02 00 00 00 00 6D  ...¨.. 8.(.....m
          0090  6F 6E 00 03 00 00 86 0C 00 00 00 00 34 EA 00 A0  on..........4ê. 
          00A0  98 00 00 00 00 00 0B 00 CB 22 00 00 20 0A 01 20  ........Ë".. .. 
          00B0  B0 04 70 02 00 00 00 00 62 68 64 00 04 00 00 06  °.p.....bhd.....
          00C0  0D 00 00 00 00 BC C5 00 A0 00 00 00 00 00 00 0B  .....¼Å. .......
          00D0  00 C3 3E 00 00 10 0F 01 20 60 09 A8 05 00 00 00  .Ã>..... `.¨....
          00E0  00 72 78 6D 00 05 00 00 02 14 00 00 00 00 00 00  .rxm............
          00F0  00 00 00 00 00 00 00 00 2F 00 72 4C 01 00 B0 18  ......../.rL..°.
          0100  01 20 50 2D 68 23 00 00 00 00 6E 61 76 00 06 00  . P-h#....nav...
          0110  00 8A 0F 01 00 00 00 90 CD 00 20 FC 32 00 00 00  ........Í. ü2...
          0120  00 00 00 B2 01 00 00 40 46 01 20 E0 06 60 02 00  ...²...@F. à.`..
          0130  00 00 00 73 66 72 00 07 00 00 06 0A 00 00 00 00  ...sfr..........
          0140  94 3B 02 20 00 00 00 00 00 00 00 00 16 00 00 00  .;. ............
          0150  60 4D 01 20 78 05 94 01 00 00 00 00 6C 70 63 00  `M. x.......lpc.
          0160  0A 00 00 86 05 00 00 00 00 18 34 02 20 D9 03 00  ..........4. Ù..
          0170  00 00 00 00 00 6B 00 00 00 48 8B 01 20 30 03 CC  .....k...H.. 0.Ì
          0180  00 00 00 00 00 66 73 00 00 0C 00 00 04 13 13 00  .....fs.........
          0190  00 00 00 00 00 00 00 00 00 00 00 00 01 00 87 06  ................
          01A0  00 00 B8 8E 01 20 10 04 F0 01 00 00 00 00 72 61  ..¸.. ..ð.....ra
          01B0  77 00 82 5D                                      w..].
          
17:35:13  0000  B5 62 0A 06 78 00 00 00 00 00 00 00 00 00 00 00  µb..x...........
          0010  00 00 00 00 00 00 00 00 00 00 00 00 00 00 00 00  ................
          0020  00 00 00 00 00 00 00 00 00 00 00 00 00 00 00 00  ................
          0030  00 00 00 00 00 00 2D 00 00 00 00 00 00 00 00 00  ......-.........
          0040  00 00 00 00 00 00 00 00 00 00 00 00 00 00 00 00  ................
          0050  00 00 00 00 00 00 00 00 00 00 00 00 00 00 00 00  ................
          0060  00 00 00 00 00 00 00 00 00 00 00 00 00 00 00 00  ................
          0070  00 00 00 00 00 00 00 00 00 00 00 00 00 00 B5 92  ..............µ..
          
17:35:13  0000  B5 62 0A 02 78 00 00 00 00 00 00 00 00 00 00 00  µb..x...........
          0010  00 00 00 00 00 00 00 00 00 00 00 00 00 00 37 05  ..............7.
          0020  00 00 00 00 00 00 00 00 00 00 01 00 00 00 00 00  ................
          0030  00 00 00 00 00 00 00 00 00 00 00 00 00 00 00 00  ................
          0040  00 00 E7 01 00 00 5F A0 81 00 00 00 00 00 00 00  ..ç..._ ........
          0050  00 00 00 01 00 00 00 00 00 00 00 00 00 00 00 00  ................
          0060  00 00 00 00 00 00 00 00 00 00 00 00 00 00 00 00  ................
          0070  00 00 00 00 00 00 00 00 00 00 00 00 00 00 2A B5  ..............*µ.
          
17:35:13  0000  B5 62 0A 26 1C 04 01 03 00 00 00 F4 52 31 00 2C  µb.&.......ôR1.,
          0010  A3 30 17 47 FA FF 6A 89 09 00 43 73 04 00 55 36  £0.Gúÿj...Cs..U6
          0020  FD FF 0E 80 10 80 0C 80 0C 80 66 0B FE 10 8F 11  ýÿ........f.þ...
          0030  D1 0A 68 0A FC 09 CA 08 7F 08 16 09 8D 09 FA 07  Ñ.h.ü.Ê.......ú.
          0040  D4 07 00 00 00 00 00 00 00 00 01 00 00 00 38 39  Ô.............89
          0050  3A 34 3A 39 36 37 39 39 3B 39 39 3C 3B 38 3C 3A  :4:96799;99<;8<:
          0060  3D 3F 3D 3F 45 42 43 45 44 44 43 4A 4A 49 4A 4A  =?=?EBCEDDCJJIJJ
          0070  49 4D 4F 53 52 55 56 54 58 5A 55 55 53 59 5C 5B  IMOSRUVTXZUUSY\[
          0080  5B 5F 5D 60 60 61 60 63 61 5F 65 64 61 65 65 62  [_]``a`ca_edaeeb
          0090  65 65 61 63 65 64 66 67 65 65 63 61 68 65 6B 69  eeacedfgeecaheki
          00A0  6D 6A 65 69 62 62 64 63 67 65 65 66 64 65 64 66  mjeibbdcgeefdedf
          00B0  64 62 62 62 64 63 63 63 63 65 63 64 64 66 69 61  dbbbdccccecddfia
          00C0  6A 66 62 69 66 64 66 66 68 6A 66 6C 63 83 65 68  jfbifdffhjflc.eh
          00D0  67 67 68 68 67 63 68 68 67 64 65 66 69 64 65 63  gghhgchhgdefidec
          00E0  65 62 65 64 66 62 66 64 63 66 66 64 66 66 65 68  ebedfbfdcffdffeh
          00F0  65 65 69 67 67 64 68 69 67 68 68 68 69 67 69 68  eeiggdhighhhigih
          0100  6B 67 67 64 67 65 65 6A 65 69 66 65 63 64 65 62  kggdgeejeifecdeb
          0110  63 66 63 61 63 61 65 61 5E 60 60 5C 5D 5F 58 57  cfcacaea^``\]_XW
          0120  58 56 56 55 52 4F 50 51 50 4D 4C 49 49 4A 4A 46  XVVUROPQPMLIIJJF
          0130  47 48 43 47 44 3E 43 3F 3E 3F 40 3F 3F 3C 42 3C  GHCGD>C?>?@??<B<
          0140  3C 3B 3D 3E 3A 3A 3F 39 3B 39 39 40 38 38 19 06  <;=>::?9;99@88..
          0150  1F 31 00 00 17 17 07 07 0A 0A 0D 0D 1B 1B 3B 3B  .1............;;
          0160  8F 8F EE EE 88 88 20 20 14 14 09 09 09 09 04 04  ..îî..  ........
          0170  03 03 00 00 0B 0B 04 04 08 08 0A 0A 09 09 29 29  ..............))
          0180  47 47 96 96 31 31 39 39 13 13 13 13 0B 0B 04 04  GG..1199........
          0190  05 05 00 00 01 01 02 02 03 03 0A 0A 11 11 23 23  ..............##
          01A0  6C 6C 4F 4F 97 97 2B 2B 18 18 06 06 06 06 01 01  llOO..++........
          01B0  01 01 00 00 00 00 02 02 04 04 0A 0A 0E 0E 24 24  ..............$$
          01C0  69 69 4E 4E A2 A2 2A 2A 11 11 0B 0B 06 06 01 01  iiNN¢¢**........
          01D0  00 00 00 00 00 00 01 01 05 05 07 07 13 13 1D 1D  ................
          01E0  69 69 5D 5D 9E 9E 25 25 12 12 07 07 05 05 03 03  ii]]..%%........
          01F0  00 00 00 00 00 00 02 02 04 04 06 06 13 13 1D 1D  ................
          0200  67 67 65 65 96 96 26 26 15 15 08 08 05 05 01 01  ggee..&&........
          0210  00 00 10 10 10 10 50 5E 10 50 00 7F F6 4D 59 88  ......P^.P..öMY.
          0220  1B 00 EC 11 1D 00 EC 11 1D 00 67 FB 28 00 3B 80  ..ì...ì...gû(.;.
          0230  88 80 1B 80 5A 80 F7 1F 3E 23 C3 1C AD 1C E0 1D  ....Z.÷.>#Ã.­.à.
          0240  04 1C 28 1C 37 1B 3B 1C 8A 1B 6F 1A 78 1B 00 00  ..(.7.;...o.x...
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

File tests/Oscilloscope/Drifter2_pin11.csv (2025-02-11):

x-axis | 1 | 2
second | Volt | Volt
-25.60000E+00
-25.57500E+00
-25.55000E+00
-25.52500E+00
-25.50000E+00
-25.47500E+00
-25.45000E+00
-25.42500E+00
-25.40000E+00
-25.37500E+00
-25.35000E+00
-25.32500E+00
-25.30000E+00
-25.27500E+00
-25.25000E+00
-25.22500E+00
-25.20000E+00
-25.17500E+00
-25.15000E+00
-25.12500E+00
-25.10000E+00
-25.07500E+00
-25.05000E+00
-25.02500E+00
-25.00000E+00 | -2.01005E+00 | +3.12274E+00
-24.97500E+00 | -1.00503E+00 | +3.47450E+00
-24.95000E+00 | -502.51E-03 | +3.21319E+00
-24.92500E+00 | +0.0E+00 | +3.21319E+00
-24.90000E+00 | -1.50754E+00 | +3.31369E+00
-24.87500E+00 | -1.00503E+00 | +3.31369E+00
-24.85000E+00 | +0.0E+00 | +3.30364E+00
-24.82500E+00 | +0.0E+00 | +3.25339E+00
-24.80000E+00 | -502.51E-03 | +3.29359E+00
-24.77500E+00 | +0.0E+00 | +3.31369E+00
-24.75000E+00 | -1.50754E+00 | +3.33379E+00
-24.72500E+00 | -2.01005E+00 | +3.29359E+00
-24.70000E+00 | +0.0E+00 | +3.26344E+00
-24.67500E+00 | +0.0E+00 | +3.33379E+00
-24.65000E+00 | -502.51E-03 | +3.39410E+00
-24.62500E+00 | -0.0E+00 | +3.29359E+00
-24.60000E+00 | +1.50754E+00 | +3.28354E+00
-24.57500E+00 | -1.00503E+00 | +3.31369E+00
-24.55000E+00 | -502.51E-03 | +3.30364E+00
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

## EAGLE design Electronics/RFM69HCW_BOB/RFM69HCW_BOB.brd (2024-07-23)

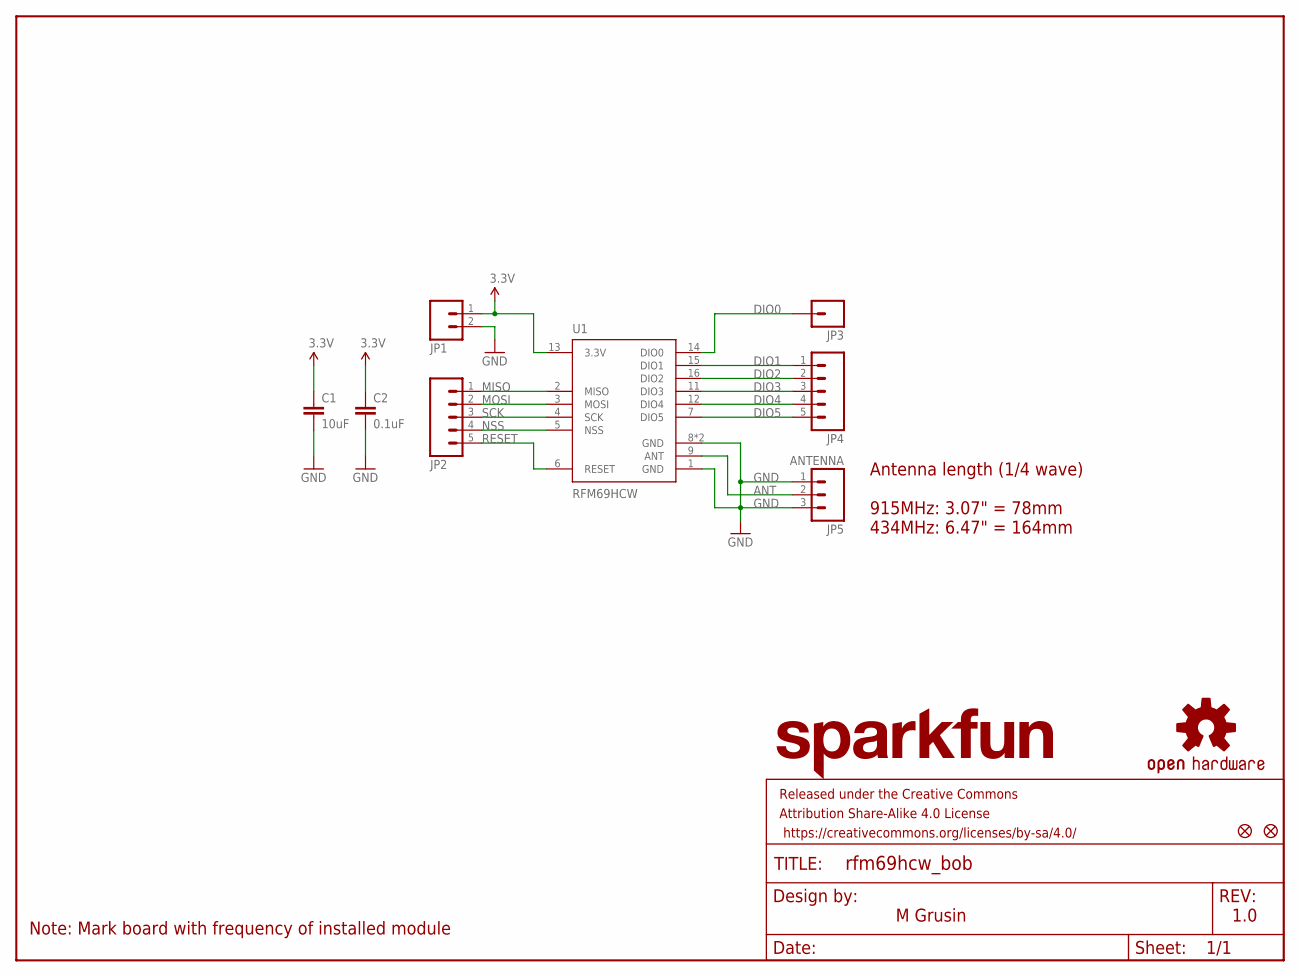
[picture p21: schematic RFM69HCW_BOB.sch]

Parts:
C1: 10uF; 1210
C2: 0.1uF; 0603-CAP
FID1, FID2: FIDUCIAL1X2; FIDUCIAL-1X2
FRAME1: FRAME-LETTER; CREATIVE_COMMONS
JP1: M021X02_NO_SILK; 1X02_NO_SILK
JP2, JP4: M05_ROUNDONLY_NOSILK; 1X05_ROUNDONLY_NOSILK
JP3: M01SMDNS; 1X01NS
JP5: ANTENNA; 1X03_ROUND_ONLY_NO_SILK
LOGO1: SFE_LOGO_NAME.1_INCH; SFE_LOGO_NAME_.1
LOGO2: OSHW-LOGOS; OSHW-LOGO-S
U1: RFM69HCW; RFM69HCW-XXXS2

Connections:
3.3V: C1.1, C2.1, JP1.1, U1.13 (3.3V)
ANT: JP5.2, U1.9 (ANT)
DIO0: JP3.1, U1.14 (DIO0)
DIO1: JP4.1, U1.15 (DIO1)
DIO2: JP4.2, U1.16 (DIO2)
DIO3: JP4.3, U1.11 (DIO3)
DIO4: JP4.4, U1.12 (DIO4)
DIO5: JP4.5, U1.7 (DIO5)
GND: C1.2, C2.2, JP1.2, JP5.1, JP5.3, U1.1 (GND), U1.8 (GND), U1.10 (GND)
MISO: JP2.1, U1.2 (MISO)
MOSI: JP2.2, U1.3 (MOSI)
NSS: JP2.4, U1.5 (NSS)
RESET: JP2.5, U1.6 (RESET)
SCK: JP2.3, U1.4 (SCK)

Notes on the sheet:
M Grusin
1.0
Note: Mark board with frequency of installed module
Antenna length (1/4 wave) 915MHz: 3.07" = 78mm 434MHz: 6.47" = 164mm

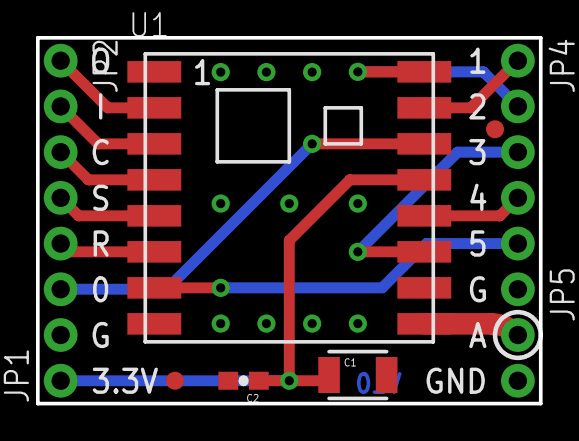
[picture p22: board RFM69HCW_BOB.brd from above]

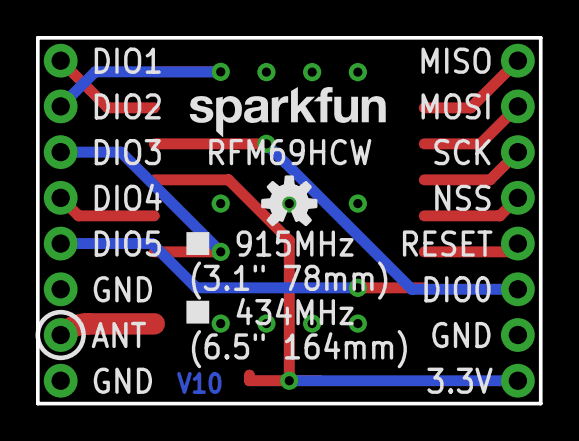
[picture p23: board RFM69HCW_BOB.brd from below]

Board: 2 copper layers, 27.9 x 20.3 mm, 13 parts (2 on the bottom side), 14 nets.

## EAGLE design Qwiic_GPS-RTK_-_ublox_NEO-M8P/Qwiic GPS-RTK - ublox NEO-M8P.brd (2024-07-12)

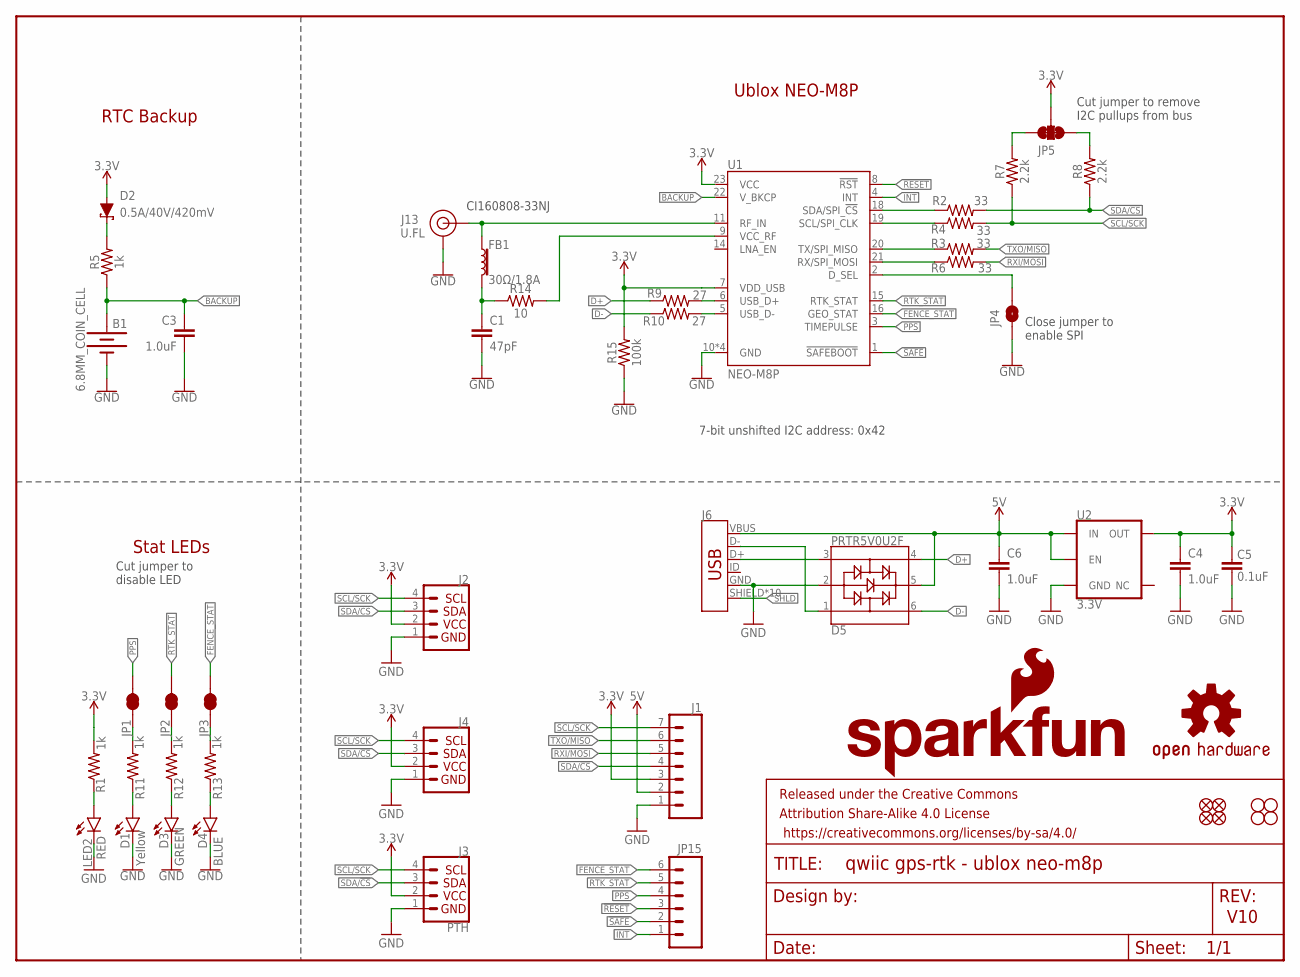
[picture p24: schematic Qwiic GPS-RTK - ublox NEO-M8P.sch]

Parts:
B1: 6.8MM_COIN_CELL; BATTCON-6.8MM
C1: 47pF; 0603
C3, C4, C6: 1.0uF; 0603
C5: 0.1uF; 0603
D1: Yellow; LED-0603
D2: 0.5A/40V/420mV; SOD-323
D3: GREEN; LED-0603
D4: BLUE; LED-0603
D5: PRTR5V0U2F; SOT886
FB1: 30Ω/1.8A; 0603
FRAME1: FRAME-LETTER; CREATIVE_COMMONS
J1: CONN_07NO_SILK; 1X07_NO_SILK
J2, J4: I2C_STANDARDQWIIC; 1X04_1MM_RA
J3: PTH; 1X04_NO_SILK
J6: USB_MICRO-B_HALF_PTH_MILL; USB-MICROB-PTH-MILL
J13: U.FL
JP1, JP2, JP3: JUMPER-SMT_2_NC_TRACE_SILK; SMT-JUMPER_2_NC_TRACE_SILK
JP4: JUMPER-SMT_2_NO_SILK; SMT-JUMPER_2_NO_SILK
JP5: JUMPER-SMT_3_2-NC_TRACE_SILK; SMT-JUMPER_3_2-NC_TRACE_SILK
JP15: M06NO_SILK_FEMALE_PTH; 1X06_NO_SILK
JP21, JP61, JP71, JP81: FIDUCIALUFIDUCIAL; MICRO-FIDUCIAL
JP31, JP41, JP91, JP101: STAND-OFF
LED2: RED; LED-0603
LOGO1: OSHW-LOGOMINI; OSHW-LOGO-MINI
LOGO2: SFE_LOGO_NAME_FLAME.1_INCH; SFE_LOGO_NAME_FLAME_.1
R1, R5, R11, R12, R13: 1k; 0603
R2, R3, R4, R6: 33; 0603
R7, R8: 2.2k; 0603
R9, R10: 27; 0603
R14: 10; 0603
R15: 100k; 0603
U1: NEO-M8P
U2: 3.3V; SOT23-5

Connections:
3.3V: C4.1, C5.2, D2.A, J1.3, J2.2, J3.2 (VCC), J4.2, JP5.2, R1.2, R15.2, U1.7 (VDD_USB), U1.23 (VCC), U2.5 (OUT)
5V: C6.1, D5.5, J1.2, J6.VBUS, U2.1 (IN), U2.3 (EN)
!RESET: JP15.3, U1.8 (!RST)
!SAFE: JP15.2, U1.1 (!SAFEBOOT!)
ANT_VCC: C1.1, FB1.2, R14.1
BACKUP: B1.+, C3.1, R5.1, U1.22 (V_BKCP)
D+: D5.4, R9.1
D-: D5.6, R10.1
D_SEL: JP4.2, U1.2 (D_SEL)
FENCE_STAT: JP3.2, JP15.6, U1.16 (GEO_STAT)
GND: B1.-, C1.2, C3.2, C4.2, C5.1, C6.2, D1.C, D3.C, D4.C, D5.2, J1.1, J2.1, J3.1 (GND), J4.1, J6.GND, J13.1 (GND), J13.2 (GND), JP4.1, LED2.C, R15.1, U1.10 (GND), U1.12 (GND), U1.13 (GND), U1.24 (GND), U2.2 (GND)
GPS_ANT1: FB1.1, J13.FEED (SIGNAL), U1.11 (RF_IN)
INT: JP15.1, U1.4 (INT)
unnamed: D3.A, R12.1
unnamed: D1.A, R11.1
unnamed: JP2.1, R12.2
unnamed: JP1.1, R11.2
unnamed: JP5.1, R8.2
unnamed: D2.C, R5.2
unnamed: D4.A, R13.1
unnamed: JP5.3, R7.2
unnamed: JP3.1, R13.2
unnamed: LED2.A, R1.1
unnamed: R9.2, U1.6 (USB_D+)
unnamed: R10.2, U1.5 (USB_D-)
unnamed: R14.2, U1.9 (VCC_RF)
PPS: JP1.2, JP15.4, U1.3 (TIMEPULSE)
RTK_STAT: JP2.2, JP15.5, U1.15 (RTK_STAT)
RXI/MOSI: J1.5, R6.2
RXLV: R6.1, U1.21 (RX/SPI_MOSI)
SCL/SCK: J1.7, J2.4, J3.4 (SCL), J4.4, R4.2, R7.1
SCL_LV: R4.1, U1.19 (SCL/SPI_CLK)
SDA/!CS: J1.4, J2.3, J3.3 (SDA), J4.3, R2.2, R8.1
SDA_LV: R2.1, U1.18 (SDA/SPI_!CS!)
SHLD: J6.SHIELD, J6.SHIELD2 (SHIELD), J6.SHIELD3 (SHIELD), J6.SHIELD4 (SHIELD), J6.SHIELD5 (SHIELD), J6.SHIELD6 (SHIELD), J6.SHIELD7 (SHIELD), J6.SHIELD8 (SHIELD), J6.SHIELD9 (SHIELD), J6.SHIELD10 (SHIELD)
TXLV: R3.1, U1.20 (TX/SPI_MISO)
TXO/MISO: J1.6, R3.2
USB_D+: D5.3, J6.D+
USB_D-: D5.1, J6.D-

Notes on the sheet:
V10
7-bit unshifted I2C address: 0x42
Ublox NEO-M8P
RTC Backup
Stat LEDs
Cut jumper to remove I2C pullups from bus
Cut jumper to disable LED
Close jumper to enable SPI
CI160808-33NJ

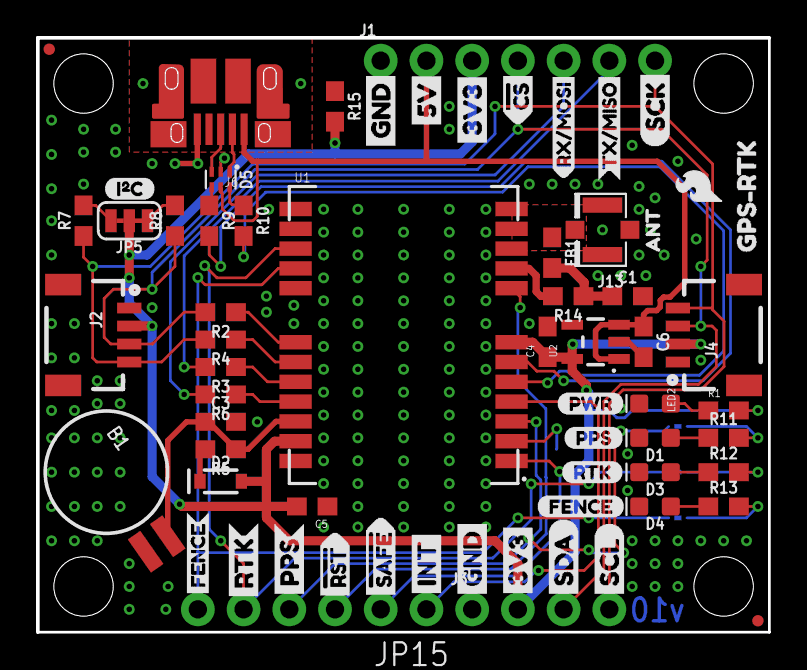
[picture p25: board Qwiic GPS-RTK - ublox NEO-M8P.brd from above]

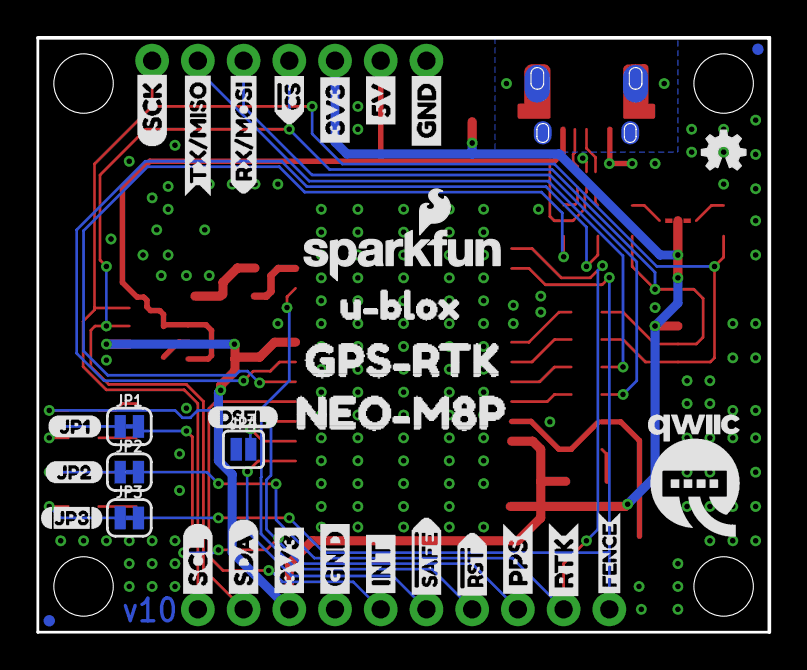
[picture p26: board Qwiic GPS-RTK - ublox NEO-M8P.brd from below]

Board: 2 copper layers, 40.6 x 33.0 mm, 103 parts (33 on the bottom side), 39 nets.

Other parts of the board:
U$1, U$4: SDA-[)
U$3, U$5: SCL-[)
U$6, U$7, U$60, U$61: 3V3-04
U$8, U$9, U$62, U$63: GND-04
U$10: I_SUPER2_C-()-03
U$11: FENCE2
U$12: JP20
U$13, U$28, U$29: RTK1
U$14, U$17: FENCE0
U$15, U$16: INT8
U$18: PWR-()-03
U$19, U$20: 5V
U$21: GPS#RTK0
U$22: U#BLOX3
U$23, U$24: CS#-<]
U$25: JP10
U$26: RX#MOSI2
U$27: DSEL0
U$30: QWIIC-LOGO-MEDIUM
U$31: RX#MOSI3
U$32: JP32
U$33: SFE_LOGO_FLAME_.1
U$34: TX#MISO0
U$35, U$36: #RST3
U$37: TX#MISO1
U$38, U$41: SCK-(]-04
U$39, U$40: #SAFE1
U$43, U$44: PPS5
U$52: PPS0
U$53: NEO#M8P3
U$54: GPS#RTK1
U$55: ANT0

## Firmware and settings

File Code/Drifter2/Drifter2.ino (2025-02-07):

/*
  Drifter 2: A water-following, Inertial-Measuring, Satellite-tracking, Position-Transceiving, wave drifter
  By: Carson Black
  Scripps Institute of Oceanography
  Date: April 19, 2024

  Hardware Connections:
  - Sparkfun GPS board Ublox NEO-M8P-2 [TAOGLAS AGGP.25F.07.0060A antenna] (I2C)
  - Pimoroni ICM20948 9DoF Motion Sensor Breakout (I2C)
  - Sparkfun RFM69HCW Wireless Transceiver - 915MHz (SPI)
  - Pololu MicroSD breakout board (SPI)
*/
#define DRIFTER2_VERSION "1.14"
#include <SPI.h>
#include <SD.h>
#include <Wire.h>
#include <elapsedMillis.h> //Flag remove extraneous libraries.  just do the math it is probably just as fast

bool debug = true; //DEBUG: TRUE enables Serial messages and extra data.
bool silent_start = true; // Disable buzzer on startup
#define PIMARONI // Define IMU
#define SparkfunGPS // Define GPS
#define SparkfunRFM // Define RFM
#define PoluluSD // Define MicroSD

/* drifter identification number */
const int drifterNumber = 1; // My node ID (1 to 254) (0 reserved for BASE STATION) (255 reserved for broadcast to ALL)
int filenumber=1;
char IMUfilename[33];
char GPSfilename[33];

/*global variables*/
float VOLTAGE = 0; // Battery voltage (V)
char DRIFTER_STATUS[4] = "STR";
unsigned long currentTime = 0;
const unsigned int IMU_UPDATE = 40; //ms //default 40ms
unsigned long lastTime_IMU = 0;
elapsedMillis sinceIMU;
const unsigned int GPS_UPDATE = 250; //ms //default 250ms //WIP GPS BINARIES LOCK IN 250ms.  Must modify to accommodate other options.
unsigned long lastTime_GPS = 0;
elapsedMillis sinceGPS;
const unsigned int RFM_UPDATE= 2000; //ms //default 8000ms
unsigned long lastTime_RFM = 0;
const unsigned int SYSTEM_UPDATE = 1000; //ms //default 1000ms
unsigned long lastTime_System = 0;

long lastlatitude = 0;
long lastlongitude = 0;
uint8_t lastUTC[4]; //FLAG.  handle UTC time offset for comms with multiple drifters
elapsedMillis sinceUTC;

const int VOLTpin = 16; // Voltage
const int LED_pin = 22;  // Indicator LED
const int recoveryLED_pin = 6;  // Recovery LED
#define runtimeLEDpower 10
const int BUZZ_pin = 1; // Buzzer
// FLAG [Drifter V2: const int BUZZ_pin = 15;]


/* IMU Variables */
#ifdef PIMARONI
  IntervalTimer IMUtimer;
  #include <ICM20948_WE.h>
  #define ICM20948_ADDR 0x68
  ICM20948_WE myIMU = ICM20948_WE(ICM20948_ADDR);
  int IMU_Write_Counter = 0;
  char accelRange[4]; //include space for null term
  char gyroRange[9];
  float xMagOffset;
  float yMagOffset;
  float zMagOffset;
  float xMagGain;
  float yMagGain;
  float zMagGain;
#endif

/* GPS variables */
#ifdef SparkfunGPS
  #include <SparkFun_u-blox_GNSS_Arduino_Library.h> //http://librarymanager/All#SparkFun_u-blox_GNSS
  #include <MicroNMEA.h>
  SFE_UBLOX_GNSS myGNSS;
  unsigned long lastGNSSsend = 0;
  #define UbloxM8P_ADDR 0x42  // Define the I2C address of the Ublox M8P chip
  char NMEA_GPSbuffer[100]; // NMEA with buffer space (u-blox_structs.h) 100 bytes is plenty 
  MicroNMEA nmea(NMEA_GPSbuffer, sizeof(NMEA_GPSbuffer)); 
  #define RAWX_GPSbuffer 3000 // Total packet size for RAWX (UBX_RXM_RAWX_MAX_LEN = 16 + (32 * 92) = 2960)
  uint16_t GPSfilebuffer = 16000; // Internal file buffer of the M8P (store messages before writing to SD card)
  uint8_t *GPSbuffer;
  const int GPS_intteruptpin = 9; // Interrupt pin ON THE TEENSY (attach ISR to this pin HIGH -> LOW)
#endif

/* RFM variables */
#ifdef SparkfunRFM
  #include <RFM69.h>
  #include <RFM69_ATC.h>
  char sendbuffer[60]; // Buffer for RFM
  const size_t sendbuffer_size = sizeof(sendbuffer); // max transmission size per packet
  int sendlength = 0; // = sizeof(sendbuffer)

  #define NETWORKID     10   // Must be the same for all nodes (0 to 255)
  #define MYNODEID      drifterNumber   // My node ID (0 to 255)
  #define BASEID      0   // Destination node ID (0 to 254, 255 = broadcast)
  #define MY_RF69_IRQ_PIN 8
  #define MY_RF69_SPI_CS 21
  #define FREQUENCY     RF69_915MHZ
  #define ENCRYPTKEY    "FILEDCREW1234567" // Use the same 16-byte key on all nodes

  struct __attribute__((packed)) RFMpayload {
      uint8_t command;    // 1 byte
      uint32_t data;      // 4 bytes
  };  // Now guaranteed to be 5 bytes
  RFMpayload RFMbuffer;
  //  Define command types
  #define CMD_MODE_MSG    0
  #define CMD_MODE_LOG    1
  #define CMD_MODE_RECOVERY 2
  #define CMD_MODE_SLEEP  3
  #define CMD_MODE_OFF    4
  #define CMD_MODE_UNKNOWN 255 //WIP?  We don't need to purposefully send this command.  But it exists on the drifter.

  // optional configs
  #define USEACK        true // Request ACKs or not
  // #define ENABLE_ATC  //comment out this line to disable AUTO TRANSMISSION CONTROL
  #define ATC_RSSI -80

  #ifdef ENABLE_ATC
  RFM69_ATC radio(MY_RF69_SPI_CS,MY_RF69_IRQ_PIN);
  #else
  RFM69 radio(MY_RF69_SPI_CS,MY_RF69_IRQ_PIN);
  #endif
#endif

/* SD variables */
File myfile;
const int SDpinCS = 5; // Pin 10 default on Teensy
char buf[100] = {'\0'}; //DEBUG - sprinf needs a buffer char to store data!  figure out how big you want this to be
// IMU buffer
const int IMUbufferSize = 50; // Adjust based on how many readings you want to buffer
// float IMUbuffer[IMUbufferSize][9]; // 9 float values per entry
// unsigned long IMUtimebuffer[IMUbufferSize];  // buffer for timestamps
char imuBuffer[IMUbufferSize][100]; // Assuming 92 chars per line
int bufferIndex = 0;

/* Debugging variables */
int time_in=0;
int time_out=0;

/* Comman Variables */
#define MAX_COMMAND_LENGTH 20
char commandBuffer[MAX_COMMAND_LENGTH];
int commandIndex=0;

/*------------------ ------------------ ------------------ ------------------ ------------------
 *                                IMU CODE Pimoroni
 * ----------------- ------------------ ------------------ ------------------ ------------------*/
#ifdef PIMARONI
 /*IMU initializtion functions*/
//this function checks that the IMU is working
void initIMU(){
  // Wire.beginTransmission(ICM20948_ADDR);
  // int error = Wire.endTransmission();
  // if(error == 0){
  //   Serial.println("ICM detected on bus");
  // }
  
  int linecount=0;
  Serial.println("waiting for ICM");
  while(!myIMU.init()){
    Serial.print(".");
    delay(50);
    linecount++;
    if(linecount==250){
      Serial.println("waiting for ICM");
      linecount=0;
    }
  }
  Serial.println("IMU initialized");

  //test Magnometer exists and works
  if(!myIMU.initMagnetometer()){
    Serial.println("ERROR: Magnetometer failed");
    while(1){}
  }
  else{
    Serial.println("Magnetometer initialized");
  }

  memset(imuBuffer, '\0', sizeof(imuBuffer)); // Set the imubuffer to null
}

void accelRangeSet(int range){
  /*choosing the argument of this functions sets the accel range and writes to the header*/
  if (range == 2){
    myIMU.setAccRange(ICM20948_ACC_RANGE_2G);
    sprintf(accelRange, "2G");
  }
  else if (range == 4){
    myIMU.setAccRange(ICM20948_ACC_RANGE_4G);
    sprintf(accelRange, "4G");
  }
  else if (range == 8){
    myIMU.setAccRange(ICM20948_ACC_RANGE_8G);
    sprintf(accelRange, "8G");
  }
  else if (range == 16){
    myIMU.setAccRange(ICM20948_ACC_RANGE_16G); 
    sprintf(accelRange, "16G");
  }
  else{
    Serial.print ("accel range error");
    while(1){}  
  }
}

void gyroRangeSet(int range){
  /*choosing the argument of this functions sets the gyro range and writes to the header*/
  if (range == 250){
    myIMU.setGyrRange(ICM20948_GYRO_RANGE_250);
    sprintf(gyroRange, "250 dps");
  }
  else if (range == 500){
    myIMU.setGyrRange(ICM20948_GYRO_RANGE_500);
    sprintf(gyroRange, "500 dps");
  }
  else if (range == 1000){
    myIMU.setGyrRange(ICM20948_GYRO_RANGE_1000);
    sprintf(gyroRange, "1000 dps");
  }
  else if (range == 2000){
    myIMU.setGyrRange(ICM20948_GYRO_RANGE_2000);
    sprintf(gyroRange, "2000 dps");
  } 
  else{
    Serial.print("gyro range error");
    while(1){}   
  }
}

//this function sets the parameters for IMU calibration and data sampling
void calibrateIMU(){
  myIMU.setAccOffsets(-16384.0, 16384.0, -16384.0, 16384.0, -16384.0, 16384.0);
  myIMU.setGyrOffsets(-29.8, 79.2, -20.0);
  xMagOffset=0;
  yMagOffset=0;
  zMagOffset=0;
  xMagGain=1.0;
  yMagGain=1.0;
  zMagGain=1.0;
  accelRangeSet(16);
  myIMU.setAccDLPF(ICM20948_DLPF_5);    
  gyroRangeSet(2000);
  myIMU.setGyrDLPF(ICM20948_DLPF_5);  
  myIMU.setTempDLPF(ICM20948_DLPF_4);
  myIMU.setMagOpMode(AK09916_CONT_MODE_20HZ);
}

// /*this function retrieves data collected by the IMU every few 
//   milliseconds and prints them to the SD card.  It is inconsistent and inefficient*/
// void gatherIMUdata(unsigned long currentTime){
//   int timer = millis(); //DEBUG
//   int timediff = 0; //DEBUG

//   myfile=SD.open(IMUfilename,FILE_WRITE);
//   myIMU.readSensor();
//   xyzFloat gValue = myIMU.getAccRawValues();
//   xyzFloat gyr = myIMU.getGyrValues();
//   xyzFloat magValue = myIMU.getMagValues();
//   float magX = xMagGain*(magValue.x-xMagOffset);
//   float magY = yMagGain*(magValue.y-yMagOffset);
//   float magZ = zMagGain*(magValue.z-zMagOffset);
//   //display current time and IMU results on the IMU file
//   memset(buf, '\0', sizeof(buf));; //clear the buffer
//   sprintf(buf,"%lu, %.1f, %.1f, %.1f, %.5f, %.5f, %.5f, %.5f, %.5f, %.5f",currentTime,gValue.x,gValue.y,gValue.z,gyr.x,gyr.y,gyr.z,magX,magY,magZ);
//   myfile.println(buf);
//   // IMU_Write_Counter++;
//   // if (IMU_Write_Counter > 200) {
//   //    myfile.flush();
//   //    IMU_Write_Counter = 0;
//   // }
//   timediff = millis() - timer;  //DEBUG
//   myfile.print("logtimer: "); //DEBUG
//   myfile.println(timediff); //DEBUG
//   myfile.flush();
//   myfile.close();
// }

void bufferIMUData(unsigned long currentTime) {
  myIMU.readSensor();
  xyzFloat gValue = myIMU.getAccRawValues();
  xyzFloat gyr = myIMU.getGyrValues();
  xyzFloat magValue = myIMU.getMagValues();
  float magX = xMagGain * (magValue.x - xMagOffset);
  float magY = yMagGain * (magValue.y - yMagOffset);
  float magZ = zMagGain * (magValue.z - zMagOffset);

  // Store in buffer
  snprintf(imuBuffer[bufferIndex], 100, "%lu, %.1f, %.1f, %.1f, %.5f, %.5f, %.5f, %.5f, %.5f, %.5f",
          currentTime, gValue.x, gValue.y, gValue.z, gyr.x, gyr.y, gyr.z, magX, magY, magZ);
  imuBuffer[bufferIndex][97] = '\0';  // New line //FLAG is this new line termination correct? will it ever write over data?
  imuBuffer[bufferIndex][98] = '\r';  // New line
  imuBuffer[bufferIndex][99] = '\n';  // Null terminate
  bufferIndex++;

  if (bufferIndex >= IMUbufferSize) {
    if(debug){
      time_in=millis();
    }
    writeIMUDataToSD();
     if(debug){
      time_out=millis()-time_in;
    }
  }
}

void writeIMUDataToSD() {
    myfile = SD.open(IMUfilename, FILE_WRITE);
  
    myfile.write((uint8_t*)imuBuffer, bufferIndex * sizeof(imuBuffer[0]));
    if (debug) {
        char timeStr[20];  // Buffer to hold the formatted time string
        sprintf(timeStr, "$%d\r\n", time_out);  // Format the time with a $ prefix and newline
        myfile.write(timeStr, strlen(timeStr));  // Write the time string to the SD card
        memset(timeStr, ' ',sizeof(timeStr)); //reset timeStr
    }

    myfile.flush();
    myfile.close();
    memset(imuBuffer, '\0', sizeof(imuBuffer)); //Wipe the buffer with ' ' char
    bufferIndex = 0;
}

// void writeIMUDataToSD() {
//     myfile = SD.open(IMUfilename, FILE_WRITE);
//     // Calculate total length of valid data in the buffer
//     int totalLength = 0;
//     for (int i = 0; i < bufferIndex; i++) {
//         totalLength += strlen(imuBuffer[i]);
//     }
//     // Write the entire valid data in one go
//     myfile.write((uint8_t*)imuBuffer, totalLength);

//     myfile.flush();
//     myfile.close();
    
//     // Reset the buffer with spaces or null characters if needed
//     memset(imuBuffer, ' ', sizeof(imuBuffer)); // Initialize with spaces to avoid unwanted characters
//     bufferIndex = 0; // Reset buffer index
// }


void flushRemainingIMUData() {
    if (bufferIndex > 0) {
        writeIMUDataToSD();
    }
}

#endif

/*------------------ ------------------ ------------------ ------------------ ------------------
 *                                GPS CODE Sparkfun/Ublox
 * ----------------- ------------------ ------------------ ------------------ ------------------*/
#ifdef SparkfunGPS
void initGPS(){
  // Configure Teensy pin as an interrupt
  pinMode(GPS_intteruptpin, INPUT);
  attachInterrupt(digitalPinToInterrupt(GPS_intteruptpin), txReadyISR, FALLING); //WIP

  if (!myGNSS.setPacketCfgPayloadSize(sizeof(NMEA_GPSbuffer) + RAWX_GPSbuffer)){
    Serial.println(F("ERROR: [GPS] setPacketCfgPayloadSize failed. You will not be able to poll RAWX data. Freezing."));
    while(1){}; // Do nothing more
  }
  myGNSS.setFileBufferSize(GPSfilebuffer);
  if (myGNSS.getFileBufferSize() != GPSfilebuffer){
    Serial.println(F("ERROR: [GPS] setFileBufferSize failed. Freezing."));
    while(1){}; // Do nothing more
  }

  // Turn the GPS on
  // Serial.println("Ready to test");
  // if (myGNSS.isConnected()) {
  //     Serial.println("GNSS module is recognized");
  //     // Now proceed to initialize
  // }
  // else{
  //   Serial.println("GNSS module is not recognized");
  // }

  for (int address = 1; address < 127; address++) {
    Wire.beginTransmission(address);
    int error = Wire.endTransmission();
    if (error == 0) {
      Serial.println(F("Device found"));
    }
    else{

    }
  }

  int linecount=0;
  Serial.println("waiting for GPS");
  while(!myGNSS.begin()){
    Serial.print(".");
    delay(250);
    linecount++;
    if(linecount==50){
      Serial.println("waiting for GPS");
      linecount=0;
    }
  }
  Serial.println("GPS initialized");

  // Configure the GPS settings
  SendGPSconfiguration(); // Use Binary to send a bunch of configurations to the M8P
  myGNSS.disableUBX7Fcheck(); // RAWX data can legitimately contain 0x7F, so we need to disable the "7F" check in checkUbloxI2C
  myGNSS.setNMEAGNGGAcallbackPtr(&printGNGGA); // Function to run when NMEA GNGGA data is received
  myGNSS.setAutoRXMRAWXcallback(&printRAWX);

  //Save settings to flash and BBR on the M8P module
  if(!myGNSS.saveConfiguration()){
    Serial.println("ERROR: [GPS] failed to save configuration");
    while(1){};
  }
  else{
    Serial.println("SUCCESS: [GPS] saved configuration");
  }
}

void printRAWX(UBX_RXM_RAWX_data_t rawxData){
  if(debug){ // print RAWX received
    Serial.print(F("\r\nRAWX: Length: "));
    Serial.print(rawxData.header.numMeas); 
  }

  // Write data to SD card
  #ifdef PoluluSD 
    int timer = millis();
    int timediff = 0;
    myfile = SD.open(GPSfilename, FILE_WRITE);  
    static char buffer[128];  // Allocate buffer.  See u-blox_structs.h for byte size info
    const size_t buffer_size = sizeof(buffer);
    // const uint16_t UBX_RXM_RAWX_MAX_LEN = 16 + (32 * 92); 92+16=118

    // Format the header data into the buffer
    double rcvTowValue;  // Convert rcvTow to double
    memcpy(&rcvTowValue, rawxData.header.rcvTow, sizeof(rcvTowValue));
    int len = snprintf(buffer, buffer_size, "%.6f,%d,%d,%d\n", 
                      rcvTowValue, 
                      rawxData.header.week, 
                      rawxData.header.leapS, 
                      rawxData.header.numMeas);
    // Write the header to the file
    if (len > 0 && len < buffer_size) {
        myfile.write(buffer, len);  // Only write the actual content, not the full buffer size
    } else { // Buffer size is too small or another error occured
      if(debug){
        Serial.print('ERROR: [GPS] cannot compose rawx file write. len = ');
        Serial.println(len);
      }
    }

    // Write block information from each Satallite
    for (int i = 0; i < rawxData.header.numMeas; i++) {
      double prMesValue, cpMesValue, doMesValue; // decode RAWX bytes into double variable
      memcpy(&prMesValue, rawxData.blocks[i].prMes, sizeof(prMesValue));
      memcpy(&cpMesValue, rawxData.blocks[i].cpMes, sizeof(cpMesValue));
      memcpy(&doMesValue, rawxData.blocks[i].doMes, sizeof(doMesValue));
      // Format the data into the buffer
      int len = snprintf(buffer, buffer_size,
                        "%d,%f,%f,%f,%d,%d,%d,%d,%d,%d,%d,%d,%d,%d,%d,%d\n",
                        i,
                        prMesValue,
                        cpMesValue,
                        doMesValue,
                        rawxData.blocks[i].gnssId,
                        rawxData.blocks[i].svId,
                        rawxData.blocks[i].sigId,
                        rawxData.blocks[i].freqId,
                        rawxData.blocks[i].lockTime,
                        rawxData.blocks[i].cno,
                        rawxData.blocks[i].prStdev,
                        rawxData.blocks[i].cpStdev,
                        rawxData.blocks[i].doStdev,
                        rawxData.blocks[i].trkStat.bits.prValid,
                        rawxData.blocks[i].trkStat.bits.cpValid,
                        rawxData.blocks[i].trkStat.bits.halfCyc,
                        rawxData.blocks[i].trkStat.bits.subHalfCyc
      );
      // Write the buffer to the file
      if (len > 0 && len < buffer_size) {
        myfile.write(buffer, len);
      }
      else{ // Buffer size is too small or another error occured
        if(debug){
          Serial.print('ERROR: [GPS] cannot compose rawx file write. len = ');
          Serial.println(len);
        }
      }
    }
    timediff = millis() - timer;  //DEBUG
    myfile.print("logtimer: "); //DEBUG
    myfile.println(timediff); //DEBUG
    myfile.flush();
    myfile.close();
    #endif
}
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
void loop() {
  // put your main code here, to run repeatedly:
  currentTime = millis();
  
  if (strcmp(DRIFTER_STATUS, "OFF") != 0) {
    if((currentTime - lastTime_System)>=SYSTEM_UPDATE){
      if(debug){
        VOLTAGE= readBatteryVoltage(1);
        Serial.print("Voltage: ");
        Serial.println(VOLTAGE);
      }
      lastTime_System=currentTime;
    }

    #ifdef SparkfunGPS
      if ((sinceGPS)>=GPS_UPDATE) {
        myGNSS.checkUblox(); // Check for the arrival of new data and process it.
        myGNSS.checkCallbacks(); // Check if any callbacks are waiting to be processed.
        // lastTime_GPS = currentTime;
        sinceGPS= sinceGPS - GPS_UPDATE;
      }
    #endif

    #ifdef PIMARONI
      if ((sinceIMU)>=IMU_UPDATE) {
        // gatherIMUdata(currentTime);
        bufferIMUData(currentTime);
        sinceIMU = sinceIMU - IMU_UPDATE;
        // Serial.print("IN IMU UPDATE time: ");   Serial.println(currentTime);
      }
    #endif

      // Send an RFM message to Base
    #ifdef SparkfunRFM
      if((currentTime - lastTime_RFM)>=RFM_UPDATE){
        int len = snprintf(sendbuffer,sendbuffer_size,"%s,%ld,%ld,%lu,%.2fV", DRIFTER_STATUS, lastlatitude, lastlongitude, (unsigned long)sinceUTC , VOLTAGE);
        
        if (len < 0) {
          if(debug) {Serial.println("ERROR: RFM broadcast message encoding failed");}
          return;
        }
        if (len >= sendbuffer_size) {
          if(debug) {Serial.println("WARNING: RFM broadcast message truncated");}
        }

        if (USEACK){
          if (radio.sendWithRetry(BASEID, sendbuffer, len < sendbuffer_size ? len : sendbuffer_size-1))
            if(debug) {Serial.println("SUCCESS: message sent to base");}
          else
            if(debug) {Serial.println("ERROR: unable to reach Base");}
        }
        else{
          radio.send(BASEID, sendbuffer, len < sendbuffer_size ? len : sendbuffer_size-1);
        }
        lastTime_RFM = currentTime;
      }
    #endif

    // Receive commands via RFM
      #ifdef SparkfunRFM
      if (radio.receiveDone()) {
      if (radio.DATALEN != sizeof(RFMbuffer)) {
        if(debug) {
          Serial.print("ERROR: DATALEN (");
          Serial.print(radio.DATALEN);
          Serial.print(") does not match sizeof(RFMpayload) (");
          Serial.print(sizeof(RFMpayload));
          Serial.println(")");
        }
      }
      else{
        RFMbuffer = *(RFMpayload*)radio.DATA;  // Copy the received data to RFMbuffer before sending ack
      }

      // Send acknowledgment back to base if needed
      if (radio.ACKRequested()) {
        radio.sendACK();
      }

      handleCommand(RFMbuffer.command, RFMbuffer.data);
      }
    #endif
  }
  else{
    //WIP
    /*
    -implement low power mode for teensy deep sleep
    -Move this if statment if you find a way to receive RFM commands while in deep sleep
    -Try Tx mode with RFM because you never know when the base will request a command
          - This is the best use case for IMU-defined wake from sleep (wave detection for listening mode vs sleep)
    */
  }
  
  if (Serial.available() > 0) {
  char input = Serial.read();
  uint8_t command = CMD_MODE_UNKNOWN;
  if(debug) {
        Serial.println();
        Serial.println("[SERIAL] MESSAGE RECEIVED");
        Serial.print("Command: ");
        Serial.println(input);
  }
  switch(input) {
    case 'L':
      command = CMD_MODE_LOG;
      break;
    case 'R':
      command = CMD_MODE_RECOVERY;
      break;
    case 'S':
      command = CMD_MODE_SLEEP;
      break;
    case 'O':
      command = CMD_MODE_OFF;
      break;
    default:
      if(debug) Serial.println("Unknown command");
      return;
  }
  handleCommand(command);
  }
}

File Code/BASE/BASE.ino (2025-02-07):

/*
  Drifter 2: A water-following, Inertial-Measuring, Sattelite-tracking, Position-Transceiving, wave drifter
  By: Carson Black
  Scripps Institute of Oceanography
  Date: April 19, 2024

  This Code is for the BASE station.  Each Drifter is configured to broadcast coordinates to node 0 on the network, the base node!
  This base station reads in telemetry from the broadcasting drifters and displays it on a field laptop.

  To-Do:
  - [x] read in broadcast strings from a drifter
  - [ ] handle broadcasts from multiple drifers (broadcast a timing command that sets each clock for broadcasting)
    - give a "token" to each drifter that gives it permission to broadcast
  - [X] relay broadcasts into external software (Mission Planner) for GPS mapping
  - [ ] [RFM] Send drifter commands
  - [ ] [RFM] Handle multiple drifter transmissions (timing)
  - [ ] interrupt based incoming transmission handling
  - [ ] Parse incoming RFM message to populate drifter

  Hardware Connections:
  - Sparkfun GPS board Ublox NEO-M8P-2 [TAOGLAS AGGP.25F.07.0060A antenna] (I2C) (Optional)
  - Sparkfun RFM69HCW Wireless Transceiver - 915MHz (SPI)
*/

#include <RFM69.h>
#include <RFM69_ATC.h>
#include <SPI.h>
#include "c_library_v2/common/mavlink.h"

bool debug = true; //DEBUG: TRUE enables Serial messages and extra data.

struct DrifterData{ // Data to capture from each Drifter RFM signal
  uint8_t drifterID;
  int32_t lat;
  int32_t lon;
  uint32_t lastUTC;
  int16_t voltage;
  char Drifter_Status[4]; // 'STR' Startup, 'LOG' (recording data), 'REC' (recovery), 'OFF' (shutdown)
  elapsedMillis sinceRFM; //track: millis() time since last RFM signal (or use UTC time since last signal)
};

#define MAX_NUM_DRIFTERS 12
DrifterData drifters[MAX_NUM_DRIFTERS];
uint8_t drifterIDi=0; // current IDX to send mssgs
uint8_t totalnumdrifters=0; // the true length of drifterIDs
DrifterData parsedData; // Temp holder for parsed data

// Timing Variables
const unsigned int heartbeat_interval= 1000;
uint32_t lastTime_heartbeat = 0; //FLAG should this be an unsigned long?


/* RFM */
#define NETWORKID     10   // Must be the same for all nodes (0 to 255)
#define MYNODEID      0   // My node ID (0 to 255)
#define TONODEID      1   // Destination node ID (0 to 254, 255 = broadcast)
#define MY_RF69_IRQ_PIN 8
#define MY_RF69_SPI_CS 21

#define FREQUENCY     RF69_915MHZ
// AES encryption
#define ENCRYPT       true // Set to "true" to use encryption
#define ENCRYPTKEY    "FILEDCREW1234567" // Use the same 16-byte key on all nodes
#define USEACK        true // Request ACKs or not
// #define ENABLE_ATC  //comment out this line to disable AUTO TRANSMISSION CONTROL
#define ATC_RSSI -80 // Target RSSI for automatic transmission power

// Create a library object for our RFM69HCW module:
#ifdef ENABLE_ATC
RFM69_ATC radio(MY_RF69_SPI_CS,MY_RF69_IRQ_PIN);
#else
RFM69 radio(MY_RF69_SPI_CS,MY_RF69_IRQ_PIN);
#endif

struct __attribute__((packed)) RFMpayload {
      uint8_t command;    // 1 byte
      uint32_t data;      // 4 bytes
  };  // Now guaranteed to be 5 bytes
  RFMpayload RFMbuffer;
  //  Define command types
  #define CMD_MODE_MSG    0
  #define CMD_MODE_LOG    1
  #define CMD_MODE_RECOVERY 2
  #define CMD_MODE_SLEEP  3
  #define CMD_MODE_OFF    4
  #define CMD_MODE_UNKNOWN 255 //WIP?  We don't need to purposefully send this command.  But it exists on the drifter.

/* MAVlink */
// MavLink Custom parameters
const char* param_names[] = {"RECOVERY_BAT_VOLTAGE_TRIGGER", "SHUTDOWN_BAT_VOLTAGE_TRIGGER"};
#define PARAM_COUNT (sizeof(param_names) / sizeof(param_names[0])) // Define PARAM_COUNT as the number of elements in the array
float param_values[PARAM_COUNT] = {3.78, 3.7};

/*------------------ ------------------ ------------------ ------------------ ------------------
 *                                Helper Functions
 * ----------------- ------------------ ------------------ ------------------ ------------------*/

bool parserfmessage(const char* rfmessage, DrifterData &drifter) {
  long lat, lon; // Temp long vars for lat/lon
  float voltage;
  int parsed = sscanf(rfmessage, "%3s,%ld,%ld,%lu,%fV", drifter.Drifter_Status, &lat, &lon, &drifter.lastUTC, &voltage);

  drifter.lat = (int32_t)(lat*10); // Assign to int32_t lat and convert to 1E7
  drifter.lon = (int32_t)(lon*10); // Assign to int32_t lon and convert to 1E7
  drifter.voltage = (int16_t)(voltage*1000); // Assign parsed variable

  if (parsed != 5) {
    Serial.print("Parsing failed. Parsed fields: ");
    Serial.println(parsed);
    return false; // Parsing failed
  }

  return (parsed == 5);
}

void updateDrifterData(uint8_t id, int32_t latitude, int32_t longitude, float battVoltage, char Drifter_Status[4]) {
  bool drifterExists = false;
  //FLAG: function relies on drifters structure being initialized.  Could be more efficient to use a point in this function

  //check if drifterID already exists
  for (uint8_t i = 0; i < MAX_NUM_DRIFTERS; i++) {
    if (drifters[i].drifterID == id) {
      drifters[i].lat = latitude;
      drifters[i].lon = longitude;
      drifters[i].voltage = battVoltage;
      // Copy Drifter_Status safely
      strncpy(drifters[i].Drifter_Status, Drifter_Status, sizeof(drifters[i].Drifter_Status) - 1);
      drifters[i].Drifter_Status[sizeof(drifters[i].Drifter_Status) - 1] = '\0'; // Ensure null termination
      drifterExists = true;
      break;
    }
  }
  // If the drifterID does not exist, add a new entry
  //FLAG: is this extraneous?  Just iterated through all drifter vals before this?
  // Should you check if it exists first and then run your iteration?
  if (!drifterExists) {
    for (uint8_t i = 0; i < 12; i++) {
      if (drifters[i].drifterID == 0) { // Check for an uninitialized slot
        drifters[i].drifterID = id;
        drifters[i].lat = latitude;
        drifters[i].lon = longitude;
        drifters[i].voltage = battVoltage;
        // Copy Drifter_Status safely
      strncpy(drifters[i].Drifter_Status, Drifter_Status, sizeof(drifters[i].Drifter_Status) - 1);
      drifters[i].Drifter_Status[sizeof(drifters[i].Drifter_Status) - 1] = '\0'; // Ensure null termination
        break;
      }
    }
  }
}

/*------------------ ------------------ ------------------ ------------------ ------------------
 *                                RFM Functions
 * ----------------- ------------------ ------------------ ------------------ ------------------*/
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

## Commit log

2024-07-12 rename folder
    [housing2_rev2_20240223.STL]
2024-07-16 Internal Cradle V5.2
    - more antenna clearance
    - wider RFM69 mount
    [Drifter2_Assem1_LOWCG.SLDASM, InternalMounts5_GPS_Cradle.SLDPRT]
2024-07-16 ignore .obsidian
    [Drifter2_Assem1_LOWCG.SLDASM, InternalMounts5_GPS_Cradle.SLDPRT, Teensy_4-0.SLDPRT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]
2024-07-16 add LED mount to GPS cradle
    [InternalMounts5_GPS_Cradle.SLDPRT]
2024-07-16 update assembly
    [Drifter2_Assem1_LOWCG.SLDASM]
2024-07-17 clean up internalmounts
    - smooth RFM leg transitionj
    - verify teensy internalmount clearance
    [Drifter2_Assem1_LOWCG.SLDASM, InternalMounts5_GPS_Cradle.SLDPRT, internalmounts.SLDPRT]
2024-07-18 Prep files for 3DP Drifter2.1
    - export STL with 3dp supports
    - update assembly to use smaller GPS ant
    - add 1W LED component
    [1W-LED_280mA_Xiaoyztan.SLDPRT, 20240718_InternalMounts5-1_GPS_Cradle-SUPPORTS.STL, 20240718_InternalMounts5-1_GPS_Cradle.STL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]
2024-07-18 saved solidworks assembly
    [Drifter2_Assem1_LOWCG.SLDASM]
2024-07-19 RFM69HCW board files (sparkfun)
    [RFM69HCW_BOB.brd, RFM69HCW_BOB.sch]
2024-07-25 add clearance for M8P buttoncell bat
    [Drifter2_Assem1_LOWCG.SLDASM, InternalMounts5_GPS_Cradle.SLDPRT, Internalmount5_housingmount.SLDPRT]
2024-08-02 Friday work
    - fix initfiles bug
    - add better RFM support
    - attempt to fix GPS bugs
    - change startup tone to use recovery LED on low power
    - change loop to work with all sensors
    [BASE.ino, Drifter2.ino]
2024-08-06 Bug fixs & Development
    - fix GPS init error (Wire.begin())
    - Change startlog
    - start writing RAWX data to SD card
    [Drifter2.ino]
2024-08-06 WORKING
    Working version of RAWX data logging and IMU logging. No RFM yet
2024-08-06 Update WIPS
    - working codebase
    - set plan for voltage divder
    - set plan for base station intergration
2024-08-13 Implement Bat Voltage monitor
    - update I2C rate to fast mode 400kHz
2024-08-13 fix voltage meter implementation
    [Drifter2.ino]
2024-10-10 "Working" Development pushed to main V1.13 (#1)
    * IMU Buffer trial 1
    - string buffer
    - could try writing binary floats for more efficiency
    * Work on IMUbuffer
    * IMUbuffer
    * IMU efficient logging only
    * Improve IMUbuffer
    * Fix IMUbuffer, enable custom commands
    - IMUbuffer timing is being recorded (which slows down writes but tells me which buffer sizes are best)
    - custom commands are registered. Shutdown command simply stops writing to the SD card
    * Update tasks
    * MavLink changes
    * update comments
    * Fix Bat voltage broadcast
    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
    [BASE.ino, Drifter2.ino, mavlink_simpledemo.ino]
2025-02-07 Overhaul Command Structure & Organize (Software V1.14) (#2)
    * Init
    * Refine heartbeat parameters
    * Working MavLink Code
    - Add RFM capability to complete
    * add notes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
    [BASE.ino, Drifter2.ino]
2025-02-11 Oscilloscope test
    [Drifter2_pin11.csv]

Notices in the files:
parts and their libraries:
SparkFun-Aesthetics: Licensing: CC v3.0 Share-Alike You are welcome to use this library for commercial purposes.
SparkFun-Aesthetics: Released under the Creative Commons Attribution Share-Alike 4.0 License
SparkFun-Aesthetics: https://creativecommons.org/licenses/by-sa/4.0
